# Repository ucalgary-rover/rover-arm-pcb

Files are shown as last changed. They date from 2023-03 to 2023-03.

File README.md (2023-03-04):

# rover-arm-pcb

A custom robot arm control PCB for the 2023 SSRT rover.

## Features
* Onboard microcontroller breakout board, like an Arduino Mega or similar
* Controls up to:
    * 7x NEMA23 stepper motors
    * 2x servo motors
    * 7x limit switches
    * A spotlight
    * Other peripherals, like grip strength load cell sensors
* Per-motor current sensing capabilities
* Integrates with off-the-shelf stepper motor drivers (TB6560) and custom circuitry for high reliability and ease of assembly

## Methodology
* PCB is designed in KiCAD v7.0.
* PCB design is used as a teaching tool, so simplicity and likelihood of success was prioritized

## Dependencies
https://github.com/Alarm-Siren/arduino-kicad-library

## Opportunities for Impovement
* Use an encoder/decoder for the EN pins, instead of using so many pins on the microcontroller.

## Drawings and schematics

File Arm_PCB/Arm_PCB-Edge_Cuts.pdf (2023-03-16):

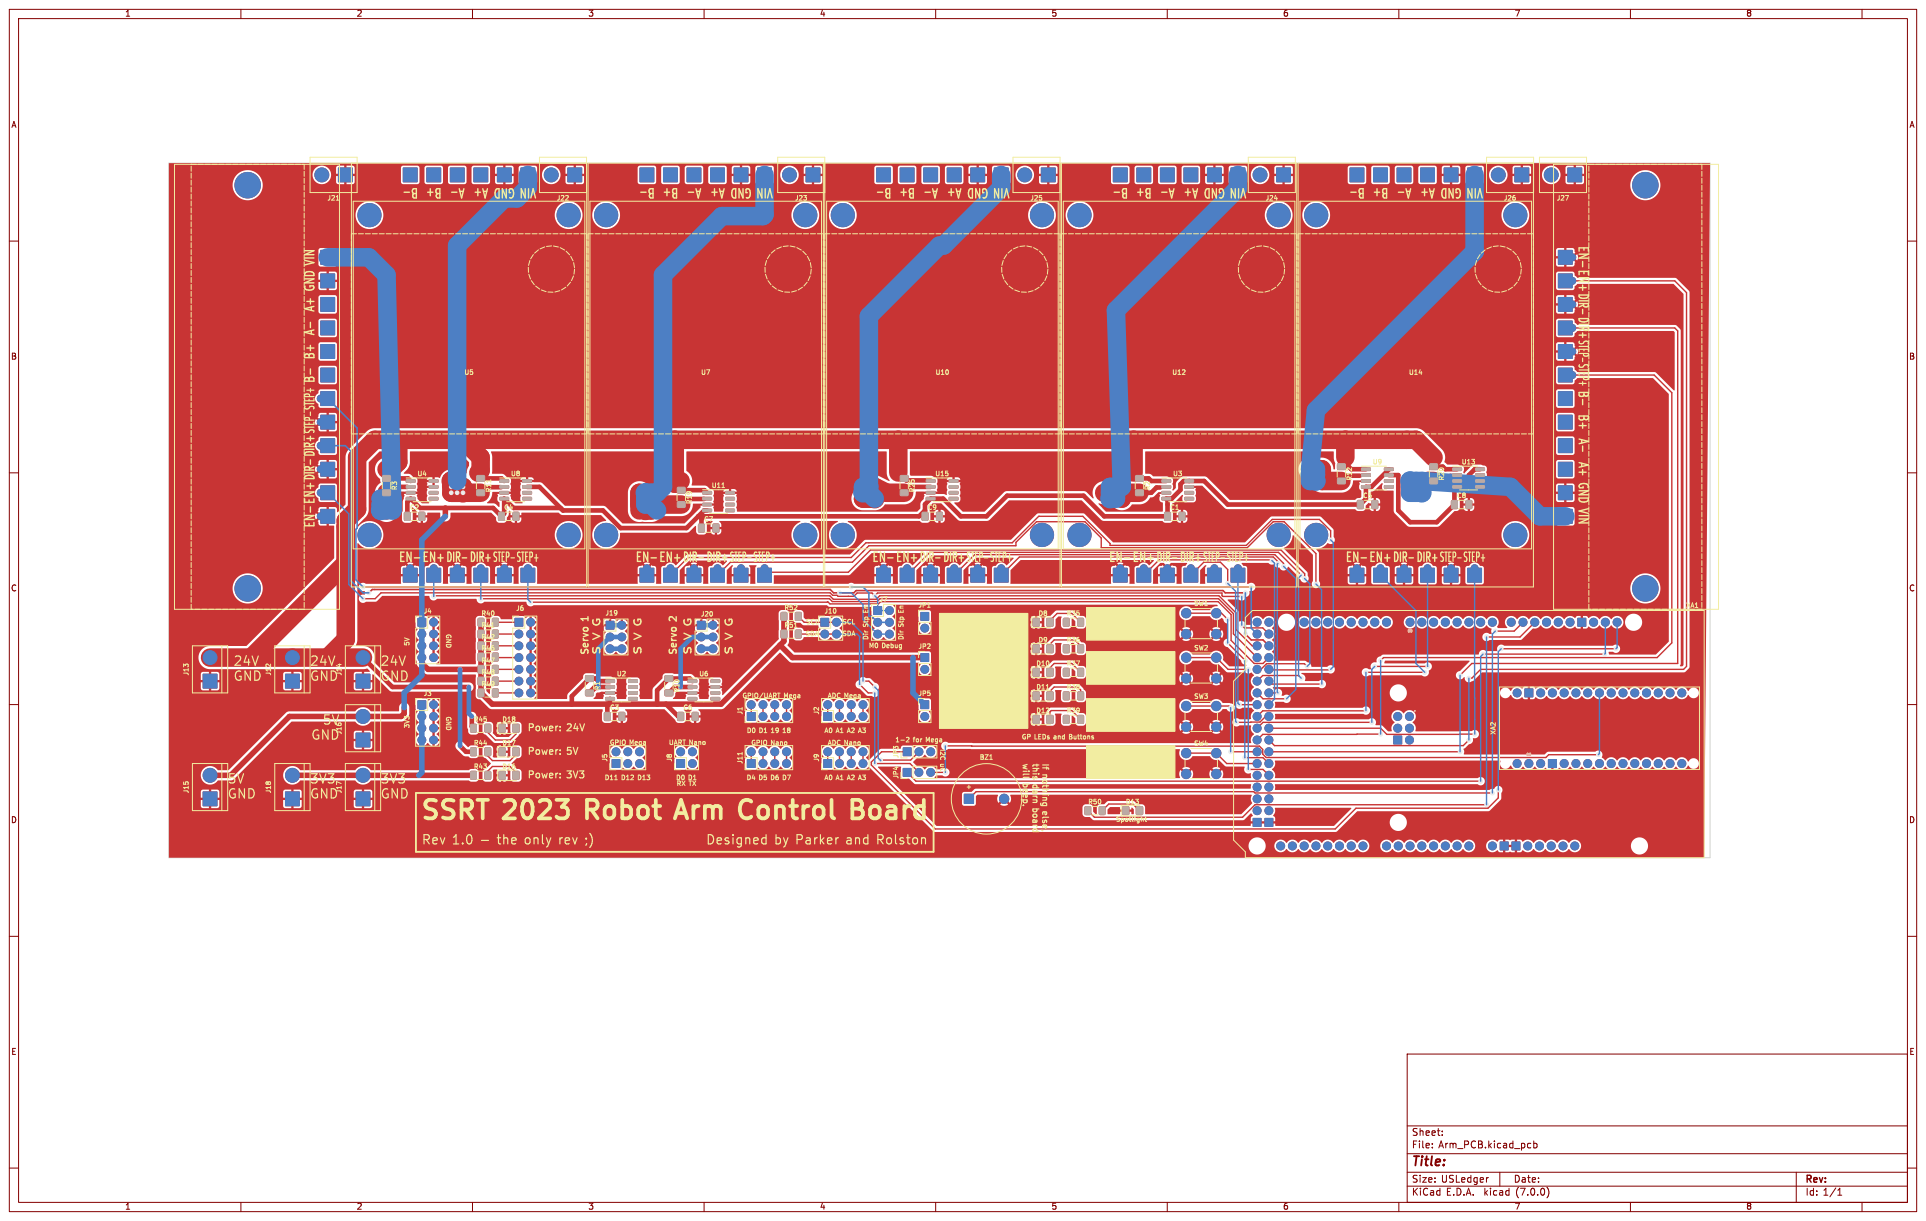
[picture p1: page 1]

R48 DIR+ B- STEP+ B+ A- EN- VIN STEP- GND A+ DIR- EN+

Id: 1/1 Title: File: Arm_PCB.kicad_pcb Sheet:

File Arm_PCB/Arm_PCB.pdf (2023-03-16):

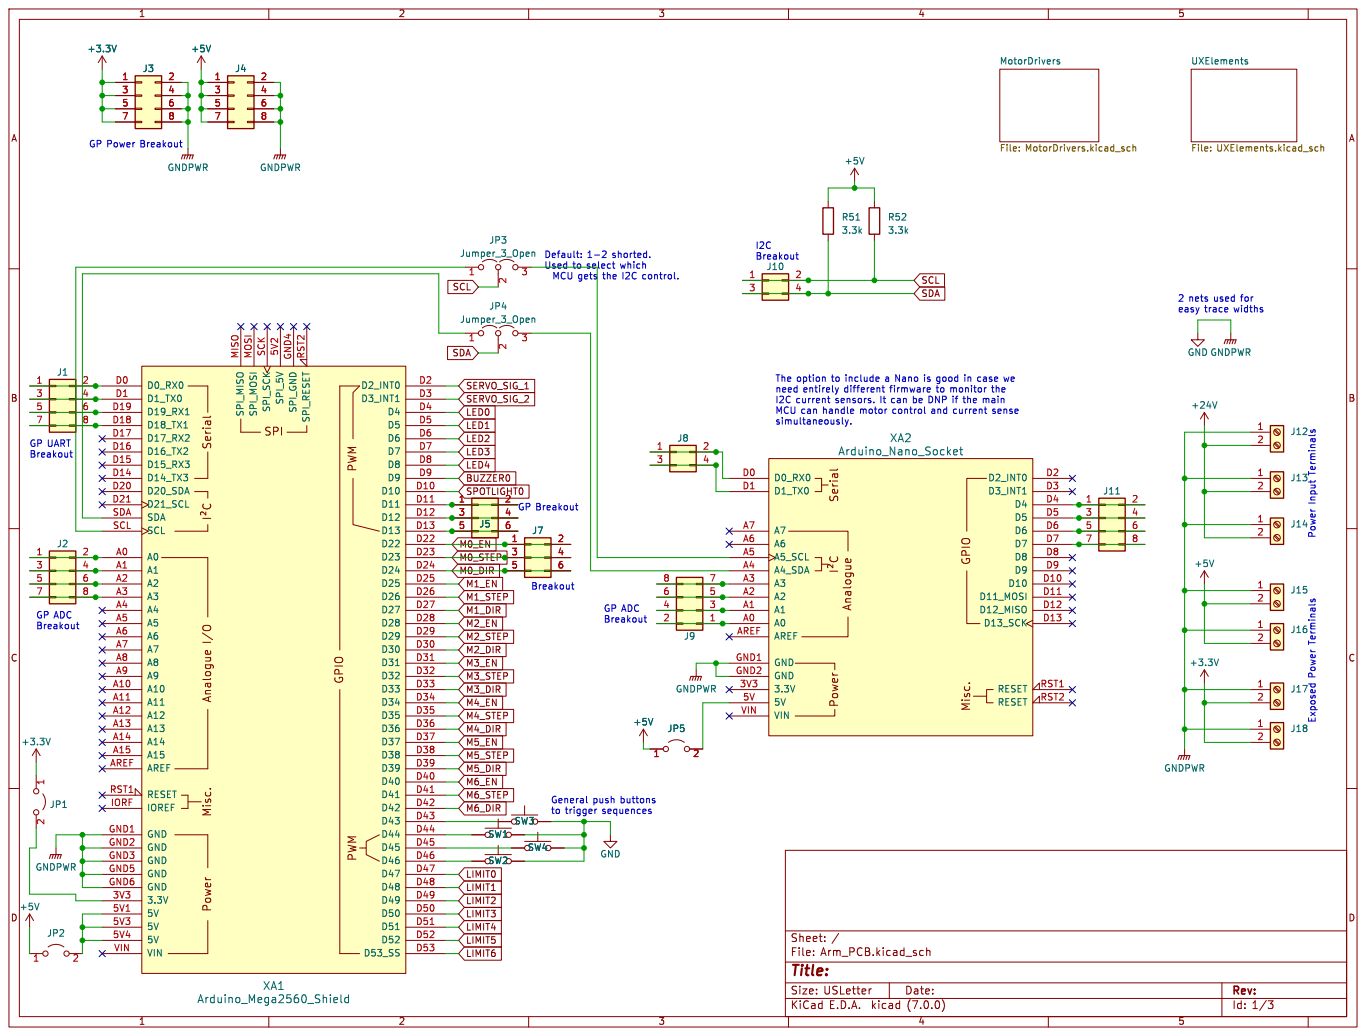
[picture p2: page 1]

GP Power Breakout GP ADC

UXElements File: UXElements.kicad_sch MotorDrivers File: MotorDrivers.kicad_sch +3.3V

I2C current sensors. It can be DNP if the main MCU can handle motor control and current sense

Id: 1/3 Title: File: Arm_PCB.kicad_sch Sheet: /

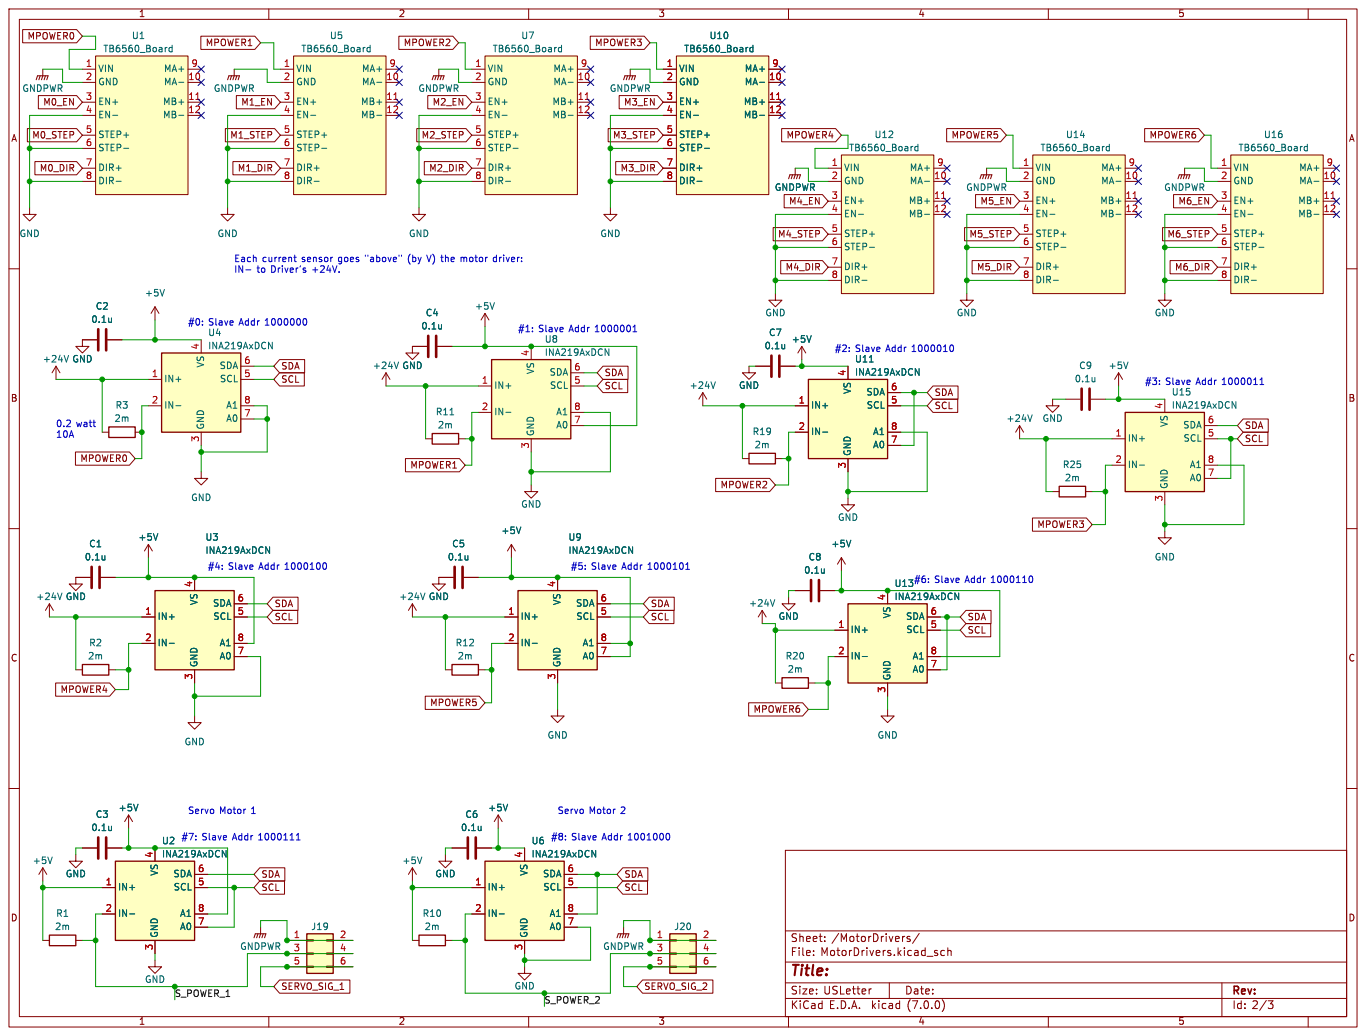
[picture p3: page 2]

#3: Slave Addr 1000011 Each current sensor goes "above" (by V) the motor driver:

#5: Slave Addr 1000101 Servo Motor 2

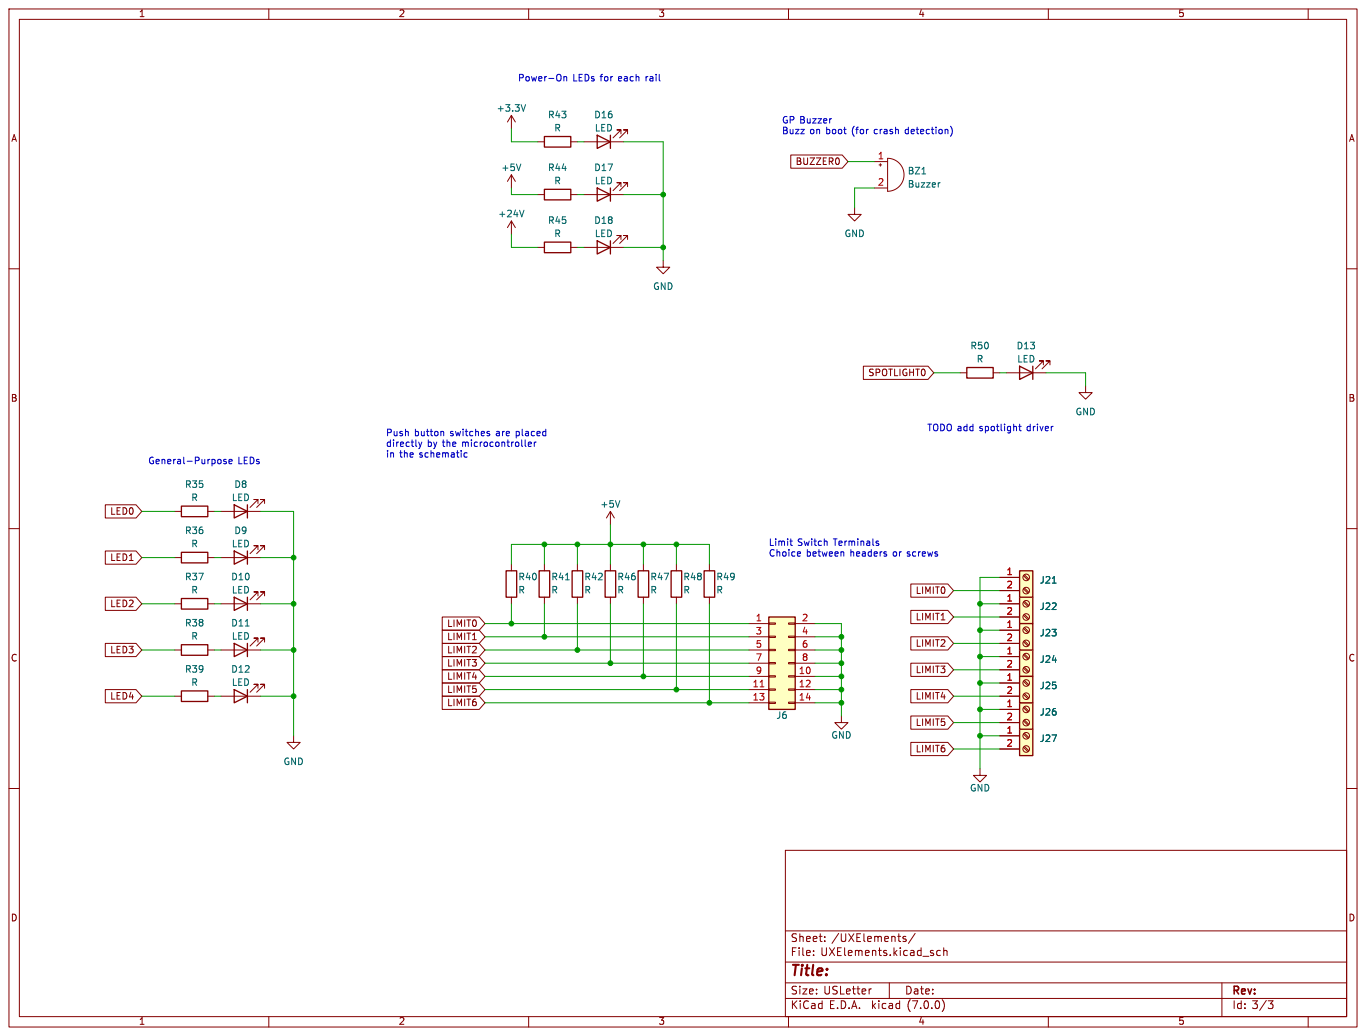
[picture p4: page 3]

directly by the microcontroller

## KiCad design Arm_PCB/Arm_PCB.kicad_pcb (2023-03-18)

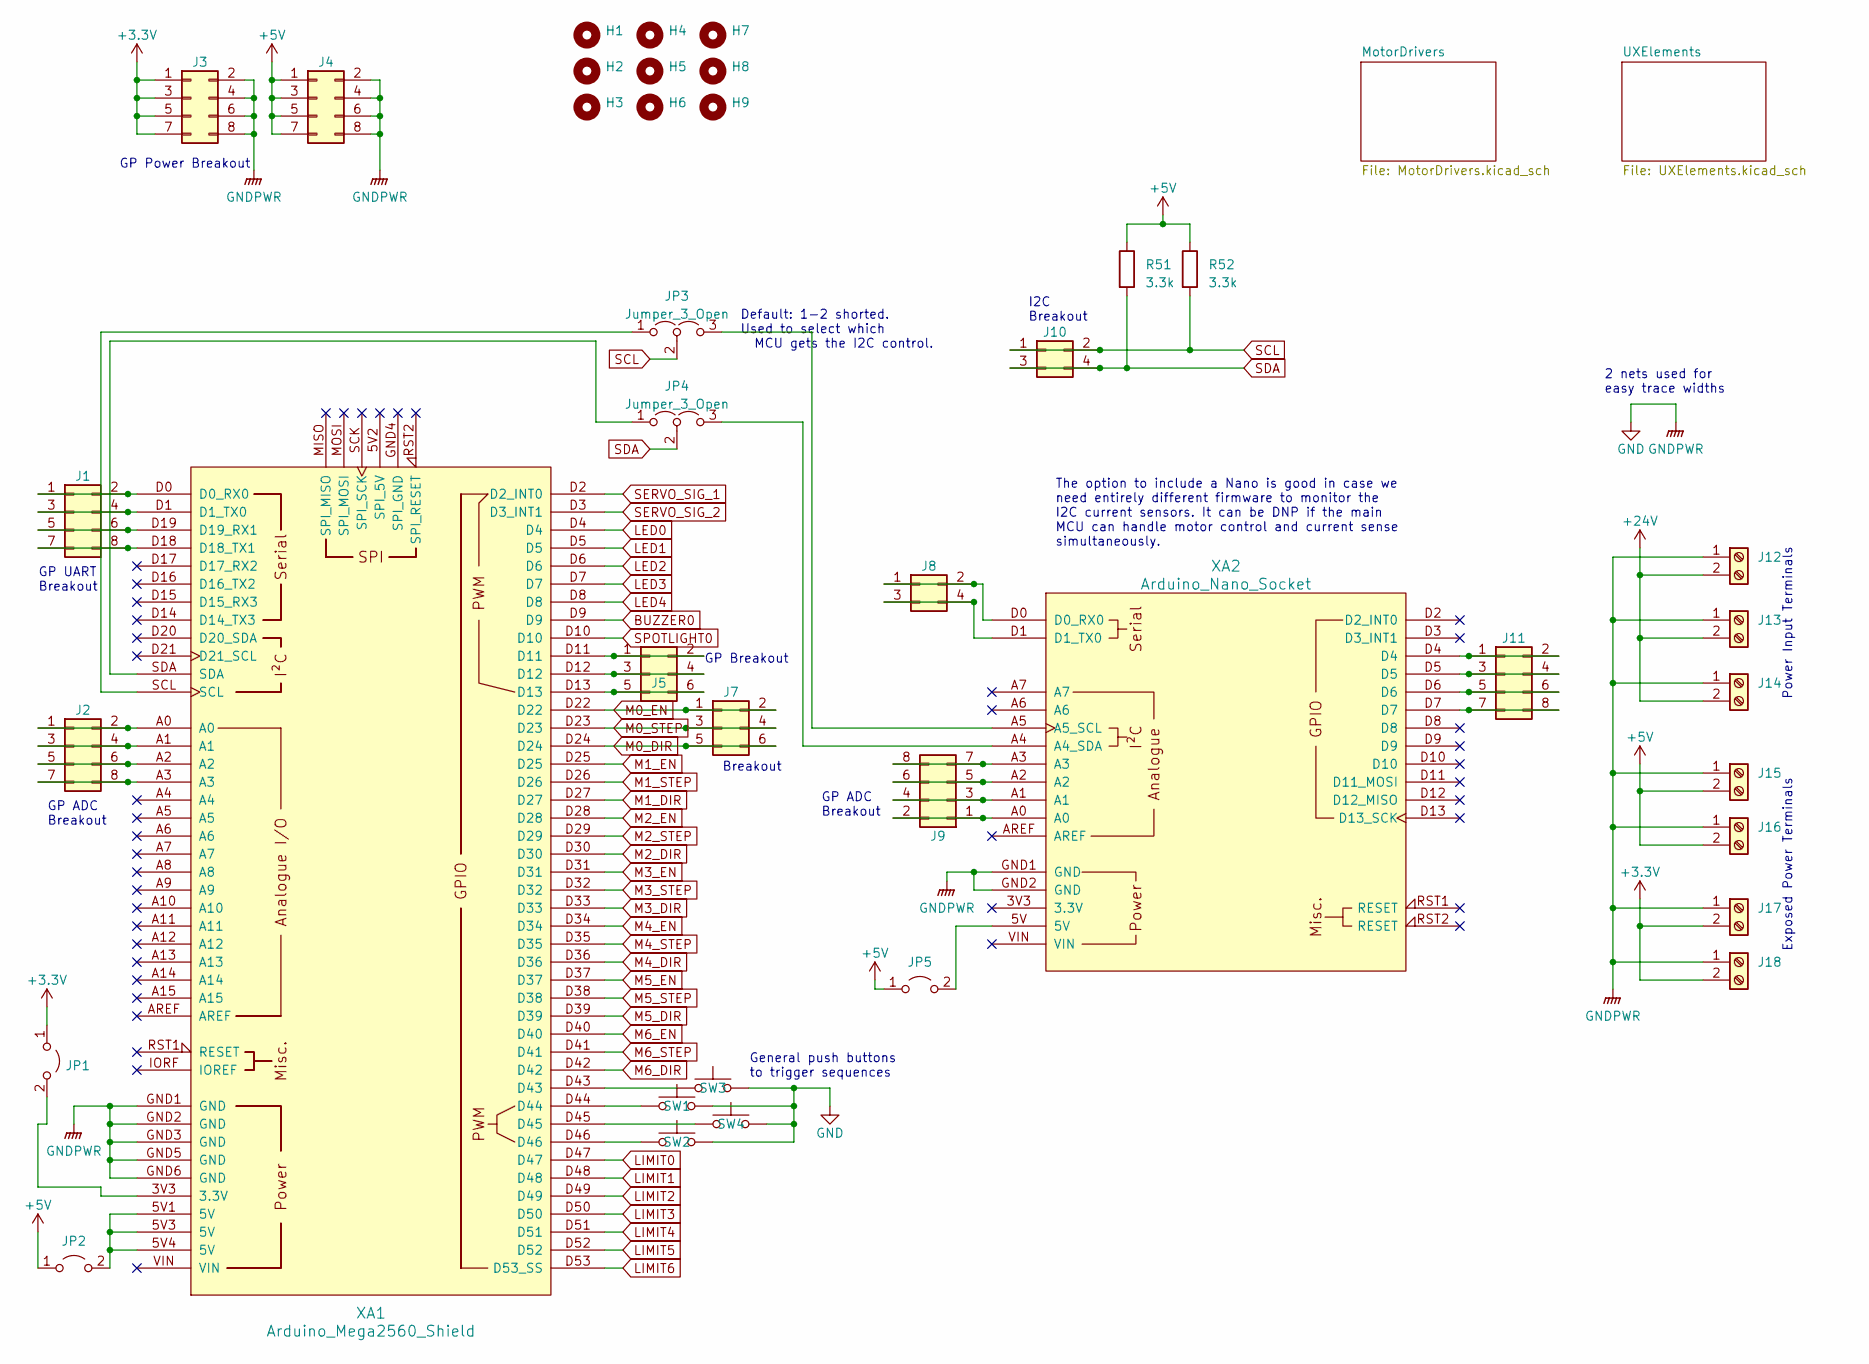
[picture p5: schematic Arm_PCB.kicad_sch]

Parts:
H1, H2, H3, H4, H5, H6, H7, H8, H9: MountingHole; MountingHole_4.3mm_M4
J1, J2, J3, J4, J9, J11: Conn_02x04_Counter_Clockwise; PinHeader_2x04_P2.54mm_Vertical
J5, J7: Conn_02x03_Counter_Clockwise; PinHeader_2x03_P2.54mm_Vertical
J8, J10: Conn_02x02_Counter_Clockwise; PinHeader_2x02_P2.54mm_Vertical
J12, J13, J14, J15, J16, J17, J18: Screw_Terminal_01x02; TerminalBlock_bornier-2_P5.08mm
JP1, JP2, JP5: Jumper_2_Open; PinHeader_1x02_P2.54mm_Vertical
JP3, JP4: Jumper_3_Open; PinHeader_1x03_P2.54mm_Vertical
R51, R52: 3.3k; R_1206_3216Metric_Pad1.30x1.75mm_HandSolder
SW1, SW2, SW3, SW4: SW_Push; SW_PUSH_6mm
XA1: Arduino_Mega2560_Shield
XA2: Arduino_Nano_Socket

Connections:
+3.3V: J3.1, J3.3, J3.5, J3.7, J17.2, J18.2, JP1.1 (A); also elsewhere on the board
+5V: J4.1, J4.3, J4.5, J4.7, J15.2, J16.2, JP2.1 (A), JP5.1 (A), R51.1, R52.1; also elsewhere on the board
+24V: J12.2, J13.2, J14.2; also elsewhere on the board
BUZZER0: XA1.D9; also elsewhere on the board
GND: J3.2, J3.4, J3.6, J3.8, J4.2, J4.4, J4.6, J4.8, J12.1, J13.1, J14.1, J15.1, J16.1, J17.1, J18.1, SW1.2, SW2.2, SW3.2, SW4.2, XA1.GND1 (GND), XA1.GND2 (GND), XA1.GND3 (GND), XA1.GND5 (GND), XA1.GND6 (GND), XA2.GND1 (GND), XA2.GND2 (GND); also elsewhere on the board
LED0: XA1.D4; also elsewhere on the board
LED1: XA1.D5; also elsewhere on the board
LED2: XA1.D6; also elsewhere on the board
LED3: XA1.D7; also elsewhere on the board
LED4: XA1.D8; also elsewhere on the board
LIMIT0: XA1.D47; also elsewhere on the board
LIMIT1: XA1.D48; also elsewhere on the board
LIMIT2: XA1.D49; also elsewhere on the board
LIMIT3: XA1.D50; also elsewhere on the board
LIMIT4: XA1.D51; also elsewhere on the board
LIMIT5: XA1.D52; also elsewhere on the board
LIMIT6: XA1.D53 (D53_SS); also elsewhere on the board
M0_DIR: J7.5, J7.6, XA1.D24; also elsewhere on the board
M0_EN: J7.1, J7.2, XA1.D22; also elsewhere on the board
M0_STEP: J7.3, J7.4, XA1.D23; also elsewhere on the board
M1_DIR: XA1.D27; also elsewhere on the board
M1_EN: XA1.D25; also elsewhere on the board
M1_STEP: XA1.D26; also elsewhere on the board
M2_DIR: XA1.D30; also elsewhere on the board
M2_EN: XA1.D28; also elsewhere on the board
M2_STEP: XA1.D29; also elsewhere on the board
M3_DIR: XA1.D33; also elsewhere on the board
M3_EN: XA1.D31; also elsewhere on the board
M3_STEP: XA1.D32; also elsewhere on the board
M4_DIR: XA1.D36; also elsewhere on the board
M4_EN: XA1.D34; also elsewhere on the board
M4_STEP: XA1.D35; also elsewhere on the board
M5_DIR: XA1.D39; also elsewhere on the board
M5_EN: XA1.D37; also elsewhere on the board
M5_STEP: XA1.D38; also elsewhere on the board
M6_DIR: XA1.D42; also elsewhere on the board
M6_EN: XA1.D40; also elsewhere on the board
M6_STEP: XA1.D41; also elsewhere on the board
unnamed: J1.1, J1.2, XA1.D0 (D0_RX0)
unnamed: J1.3, J1.4, XA1.D1 (D1_TX0)
unnamed: J1.5, J1.6, XA1.D19 (D19_RX1)
unnamed: J1.7, J1.8, XA1.D18 (D18_TX1)
unnamed: J2.1, J2.2, XA1.A0
unnamed: J2.3, J2.4, XA1.A1
unnamed: J2.5, J2.6, XA1.A2
unnamed: J2.7, J2.8, XA1.A3
unnamed: J5.1, J5.2, XA1.D11
unnamed: J5.3, J5.4, XA1.D12
unnamed: J5.5, J5.6, XA1.D13
unnamed: J8.1, J8.2, XA2.D0 (D0_RX0)
unnamed: J8.3, J8.4, XA2.D1 (D1_TX0)
unnamed: J9.1, J9.2, XA2.A0
unnamed: J9.3, J9.4, XA2.A1
unnamed: J9.5, J9.6, XA2.A2
unnamed: J9.7, J9.8, XA2.A3
unnamed: J11.1, J11.2, XA2.D4
unnamed: J11.3, J11.4, XA2.D5
unnamed: J11.5, J11.6, XA2.D6
unnamed: J11.7, J11.8, XA2.D7
unnamed: JP1.2 (B), XA1.3V3 (3.3V)
unnamed: JP2.2 (B), XA1.5V1 (5V), XA1.5V3 (5V), XA1.5V4 (5V)
unnamed: JP3.1 (A), XA1.SCL
unnamed: JP3.3 (B), XA2.A5 (A5_SCL)
unnamed: JP4.1 (A), XA1.SDA
unnamed: JP4.3 (B), XA2.A4 (A4_SDA)
unnamed: JP5.2 (B), XA2.5V
unnamed: SW1.1, XA1.D44
unnamed: SW2.1, XA1.D46
unnamed: SW3.1, XA1.D43
unnamed: SW4.1, XA1.D45
SCL: J10.1, J10.2, JP3.2 (C), R52.2; also elsewhere on the board
SDA: J10.3, J10.4, JP4.2 (C), R51.2; also elsewhere on the board
SERVO_SIG_1: XA1.D2 (D2_INT0); also elsewhere on the board
SERVO_SIG_2: XA1.D3 (D3_INT1); also elsewhere on the board
SPOTLIGHT0: XA1.D10; also elsewhere on the board

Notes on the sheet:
Exposed Power Terminals
The option to include a Nano is good in case we need entirely different firmware to monitor the I2C current sensors. It can be DNP if the main MCU can handle motor control and current sense simultaneously.
General push buttons to trigger sequences
GP UART Breakout
GP Breakout
Default: 1-2 shorted. Used to select which MCU gets the I2C control.
2 nets used for easy trace widths
GP Power Breakout
GP ADC Breakout
I2C Breakout
Breakout
Power Input Terminals

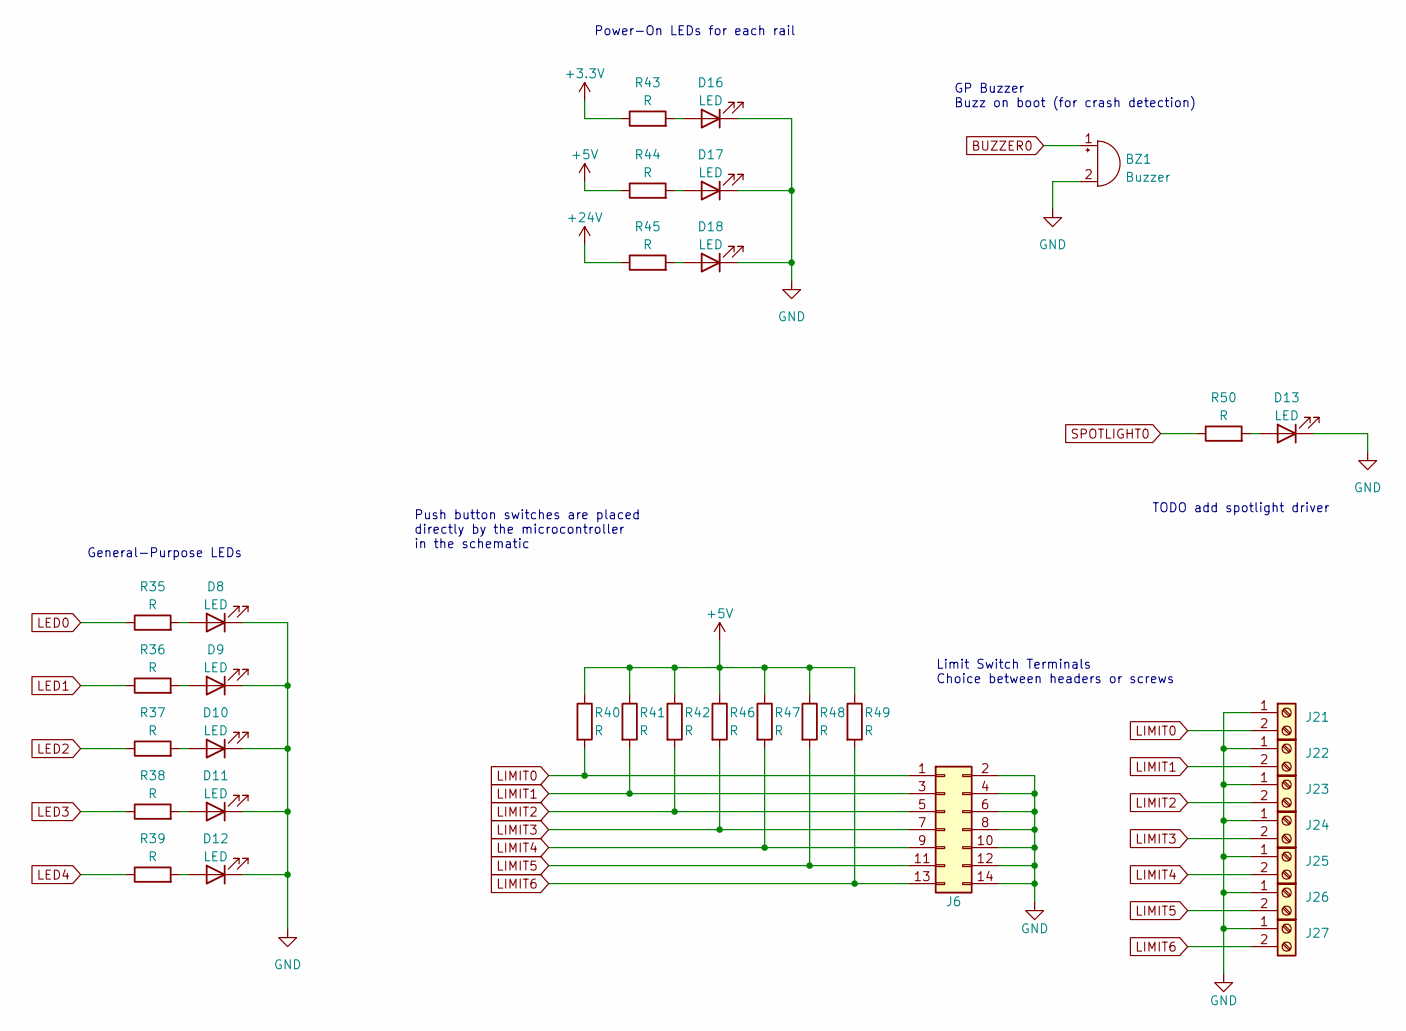
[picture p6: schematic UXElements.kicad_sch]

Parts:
BZ1: Buzzer; Buzzer_15x7.5RM7.6
D8, D9, D10, D11, D12, D13, D16, D17, D18: LED; LED_1206_3216Metric_Pad1.42x1.75mm_HandSolder
J6: Conn_02x07_Counter_Clockwise; PinHeader_2x07_P2.54mm_Vertical
J21, J22, J23, J24, J25, J26, J27: Screw_Terminal_01x02; TerminalBlock_bornier-2_P5.08mm
R35, R36, R37, R38, R39, R40, R41, R42, R43, R44, R45, R46, R47, R48, R49, R50: R; R_1206_3216Metric_Pad1.30x1.75mm_HandSolder

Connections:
+3.3V: R43.1; also elsewhere on the board
+5V: R40.1, R41.1, R42.1, R44.1, R46.1, R47.1, R48.1, R49.1; also elsewhere on the board
+24V: R45.1; also elsewhere on the board
BUZZER0: BZ1.1 (-); also elsewhere on the board
GND: BZ1.2 (+), D8.1 (K), D9.1 (K), D10.1 (K), D11.1 (K), D12.1 (K), D13.1 (K), D16.1 (K), D17.1 (K), D18.1 (K), J6.2, J6.4, J6.6, J6.8, J6.10, J6.12, J6.14, J21.1, J22.1, J23.1, J24.1, J25.1, J26.1, J27.1; also elsewhere on the board
LED0: R35.1; also elsewhere on the board
LED1: R36.1; also elsewhere on the board
LED2: R37.1; also elsewhere on the board
LED3: R38.1; also elsewhere on the board
LED4: R39.1; also elsewhere on the board
LIMIT0: J6.1, J21.2, R40.2; also elsewhere on the board
LIMIT1: J6.3, J22.2, R41.2; also elsewhere on the board
LIMIT2: J6.5, J23.2, R42.2; also elsewhere on the board
LIMIT3: J6.7, J24.2, R46.2; also elsewhere on the board
LIMIT4: J6.9, J25.2, R47.2; also elsewhere on the board
LIMIT5: J6.11, J26.2, R48.2; also elsewhere on the board
LIMIT6: J6.13, J27.2, R49.2; also elsewhere on the board
unnamed: D8.2 (A), R35.2
unnamed: D9.2 (A), R36.2
unnamed: D10.2 (A), R37.2
unnamed: D11.2 (A), R38.2
unnamed: D12.2 (A), R39.2
unnamed: D13.2 (A), R50.2
unnamed: D16.2 (A), R43.2
unnamed: D17.2 (A), R44.2
unnamed: D18.2 (A), R45.2
SPOTLIGHT0: R50.1; also elsewhere on the board

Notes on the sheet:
Push button switches are placed directly by the microcontroller in the schematic
Power-On LEDs for each rail
TODO add spotlight driver
Limit Switch Terminals Choice between headers or screws
GP Buzzer Buzz on boot (for crash detection)
General-Purpose LEDs

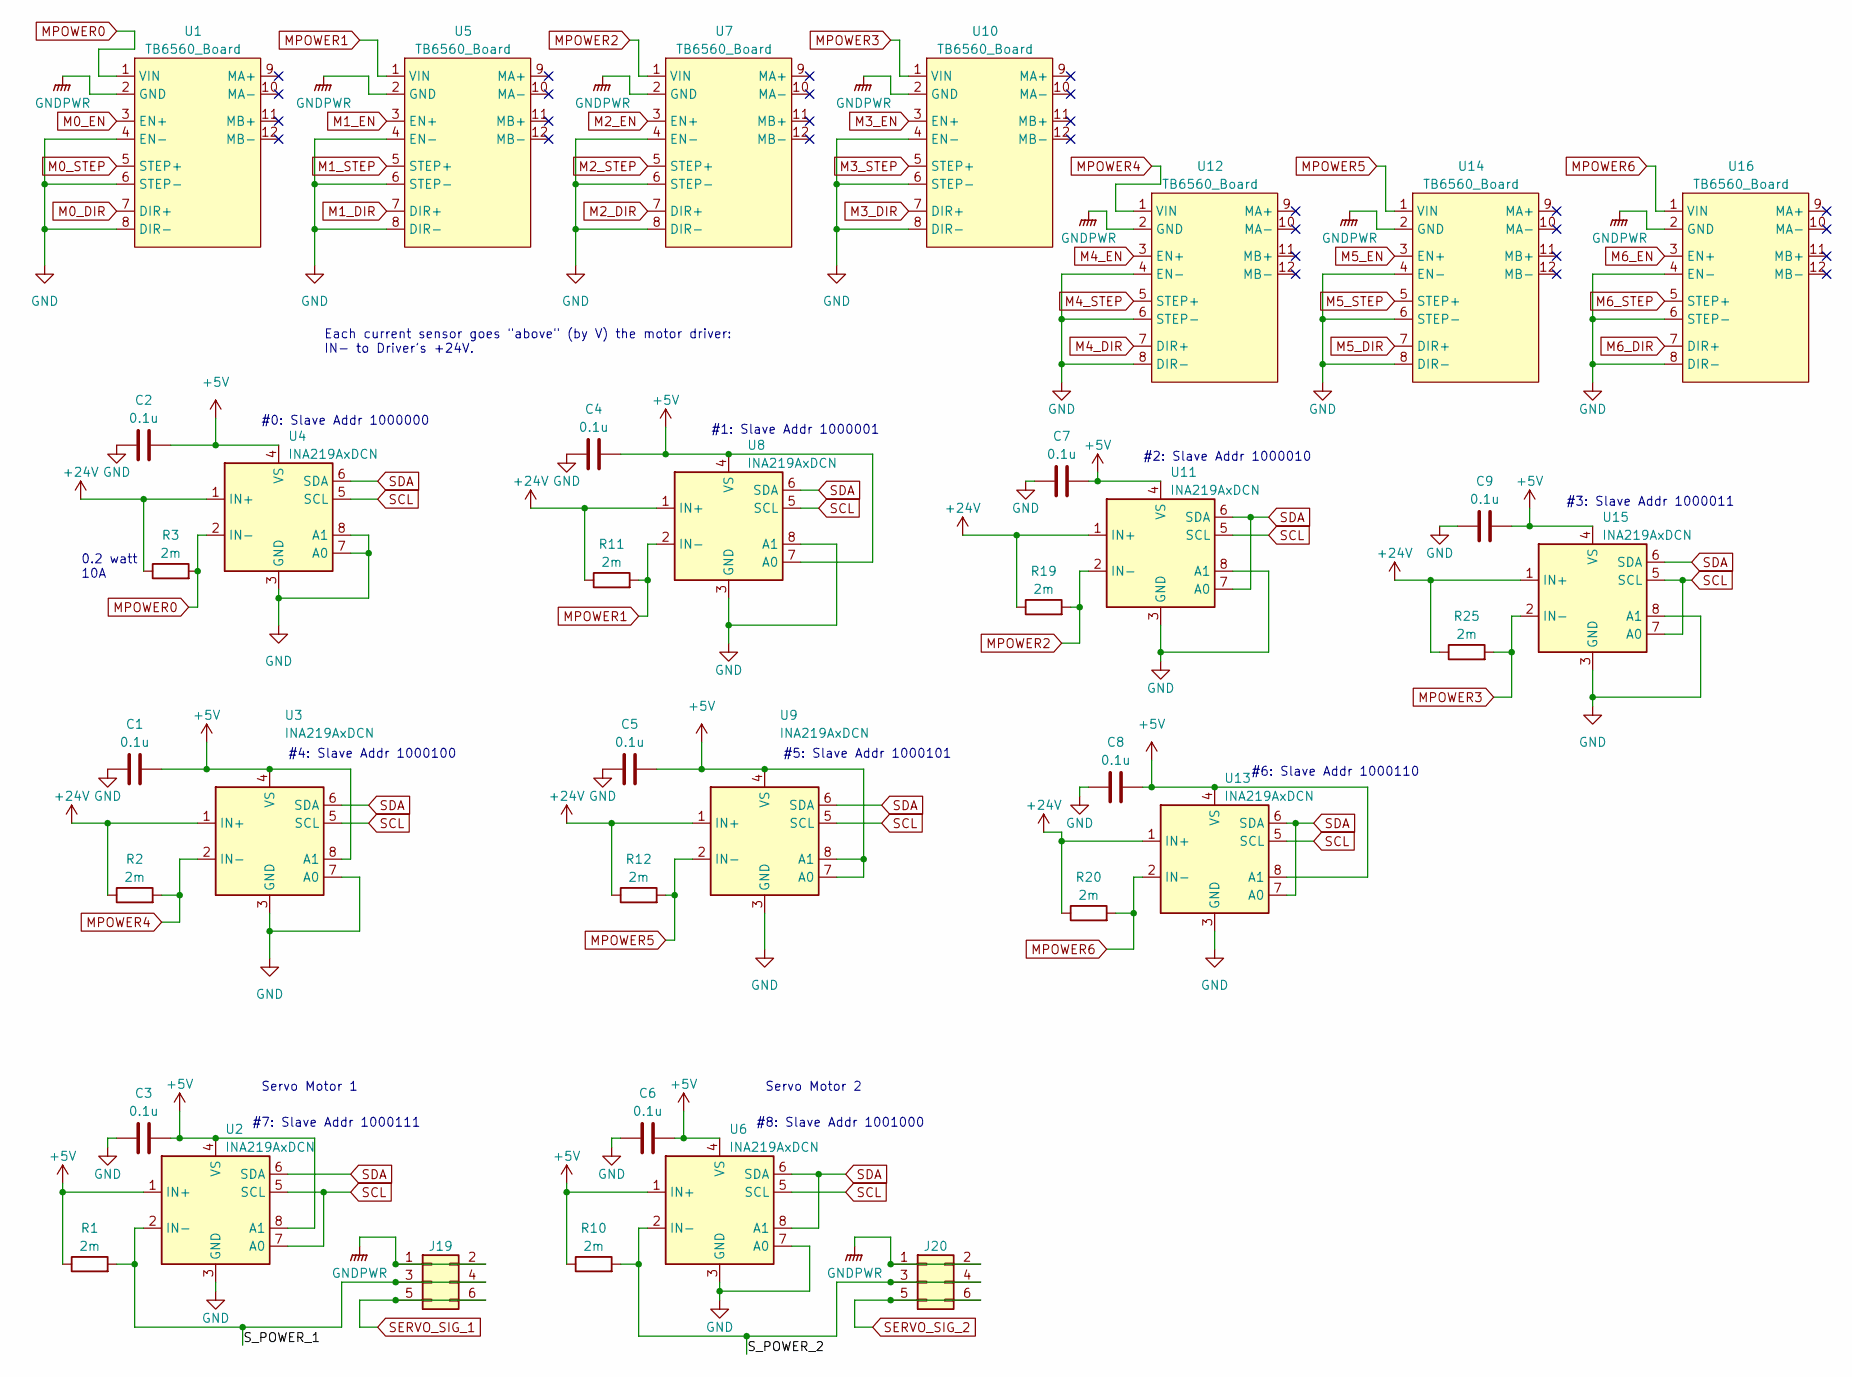
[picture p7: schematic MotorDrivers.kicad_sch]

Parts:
C1, C2, C3, C4, C5, C6, C7, C8, C9: 0.1u; C_1206_3216Metric_Pad1.33x1.80mm_HandSolder
J19, J20: Conn_02x03_Counter_Clockwise; PinHeader_2x03_P2.54mm_Vertical
R1, R2, R3, R10, R11, R12, R19, R20, R25: 2m; R_1206_3216Metric_Pad1.30x1.75mm_HandSolder
U1, U16: TB6560_Board; TB6600_Breakout
U2, U3, U4, U6, U8, U9, U11, U13, U15: INA219AxDCN; SOIC-8_3.9x4.9mm_P1.27mm
U5, U7, U10, U12, U14: TB6560_Board; TB6560_Breakout

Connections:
+5V: C1.1, C2.1, C3.1, C4.1, C5.1, C6.1, C7.1, C8.1, C9.1, R1.1, R10.1, U2.1 (IN+), U2.4 (VS), U2.8 (A1), U3.4 (VS), U3.8 (A1), U4.4 (VS), U6.1 (IN+), U6.4 (VS), U8.4 (VS), U8.7 (A0), U9.4 (VS), U9.7 (A0), U9.8 (A1), U11.4 (VS), U13.4 (VS), U13.8 (A1), U15.4 (VS); also elsewhere on the board
+24V: R2.1, R3.1, R11.1, R12.1, R19.1, R20.1, R25.1, U3.1 (IN+), U4.1 (IN+), U8.1 (IN+), U9.1 (IN+), U11.1 (IN+), U13.1 (IN+), U15.1 (IN+); also elsewhere on the board
/MotorDrivers/S_POWER_1: J19.3, J19.4, R1.2, U2.2 (IN-)
/MotorDrivers/S_POWER_2: J20.3, J20.4, R10.2, U6.2 (IN-)
GND: C1.2, C2.2, C3.2, C4.2, C5.2, C6.2, C7.2, C8.2, C9.2, J19.1, J19.2, J20.1, J20.2, U1.2 (GND), U1.4 (EN-), U1.6 (STEP-), U1.8 (DIR-), U2.3 (GND), U3.3 (GND), U3.7 (A0), U4.3 (GND), U4.7 (A0), U4.8 (A1), U5.2 (GND), U5.4 (EN-), U5.6 (STEP-), U5.8 (DIR-), U6.3 (GND), U6.7 (A0), U7.2 (GND), U7.4 (EN-), U7.6 (STEP-), U7.8 (DIR-), U8.3 (GND), U8.8 (A1), U9.3 (GND), U10.2 (GND), U10.4 (EN-), U10.6 (STEP-), U10.8 (DIR-), U11.3 (GND), U11.8 (A1), U12.2 (GND), U12.4 (EN-), U12.6 (STEP-), U12.8 (DIR-), U13.3 (GND), U14.2 (GND), U14.4 (EN-), U14.6 (STEP-), U14.8 (DIR-), U15.3 (GND), U15.8 (A1), U16.2 (GND), U16.4 (EN-), U16.6 (STEP-), U16.8 (DIR-); also elsewhere on the board
M0_DIR: U1.7 (DIR+); also elsewhere on the board
M0_EN: U1.3 (EN+); also elsewhere on the board
M0_STEP: U1.5 (STEP+); also elsewhere on the board
M1_DIR: U5.7 (DIR+); also elsewhere on the board
M1_EN: U5.3 (EN+); also elsewhere on the board
M1_STEP: U5.5 (STEP+); also elsewhere on the board
M2_DIR: U7.7 (DIR+); also elsewhere on the board
M2_EN: U7.3 (EN+); also elsewhere on the board
M2_STEP: U7.5 (STEP+); also elsewhere on the board
M3_DIR: U10.7 (DIR+); also elsewhere on the board
M3_EN: U10.3 (EN+); also elsewhere on the board
M3_STEP: U10.5 (STEP+); also elsewhere on the board
M4_DIR: U12.7 (DIR+); also elsewhere on the board
M4_EN: U12.3 (EN+); also elsewhere on the board
M4_STEP: U12.5 (STEP+); also elsewhere on the board
M5_DIR: U14.7 (DIR+); also elsewhere on the board
M5_EN: U14.3 (EN+); also elsewhere on the board
M5_STEP: U14.5 (STEP+); also elsewhere on the board
M6_DIR: U16.7 (DIR+); also elsewhere on the board
M6_EN: U16.3 (EN+); also elsewhere on the board
M6_STEP: U16.5 (STEP+); also elsewhere on the board
MPOWER0: R3.2, U1.1 (VIN), U4.2 (IN-)
MPOWER1: R11.2, U5.1 (VIN), U8.2 (IN-)
MPOWER2: R19.2, U7.1 (VIN), U11.2 (IN-)
MPOWER3: R25.2, U10.1 (VIN), U15.2 (IN-)
MPOWER4: R2.2, U3.2 (IN-), U12.1 (VIN)
MPOWER5: R12.2, U9.2 (IN-), U14.1 (VIN)
MPOWER6: R20.2, U13.2 (IN-), U16.1 (VIN)
SCL: U2.5 (SCL), U2.7 (A0), U3.5 (SCL), U4.5 (SCL), U6.5 (SCL), U8.5 (SCL), U9.5 (SCL), U11.5 (SCL), U13.5 (SCL), U15.5 (SCL), U15.7 (A0); also elsewhere on the board
SDA: U2.6 (SDA), U3.6 (SDA), U4.6 (SDA), U6.6 (SDA), U6.8 (A1), U8.6 (SDA), U9.6 (SDA), U11.6 (SDA), U11.7 (A0), U13.6 (SDA), U13.7 (A0), U15.6 (SDA); also elsewhere on the board
SERVO_SIG_1: J19.5, J19.6; also elsewhere on the board
SERVO_SIG_2: J20.5, J20.6; also elsewhere on the board

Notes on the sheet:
#1: Slave Addr 1000001
Servo Motor 2
Each current sensor goes "above" (by V) the motor driver: IN- to Driver's +24V.
Servo Motor 1
#8: Slave Addr 1001000
#0: Slave Addr 1000000
0.2 watt 10A
#7: Slave Addr 1000111
#6: Slave Addr 1000110
#2: Slave Addr 1000010
#3: Slave Addr 1000011
#5: Slave Addr 1000101
#4: Slave Addr 1000100

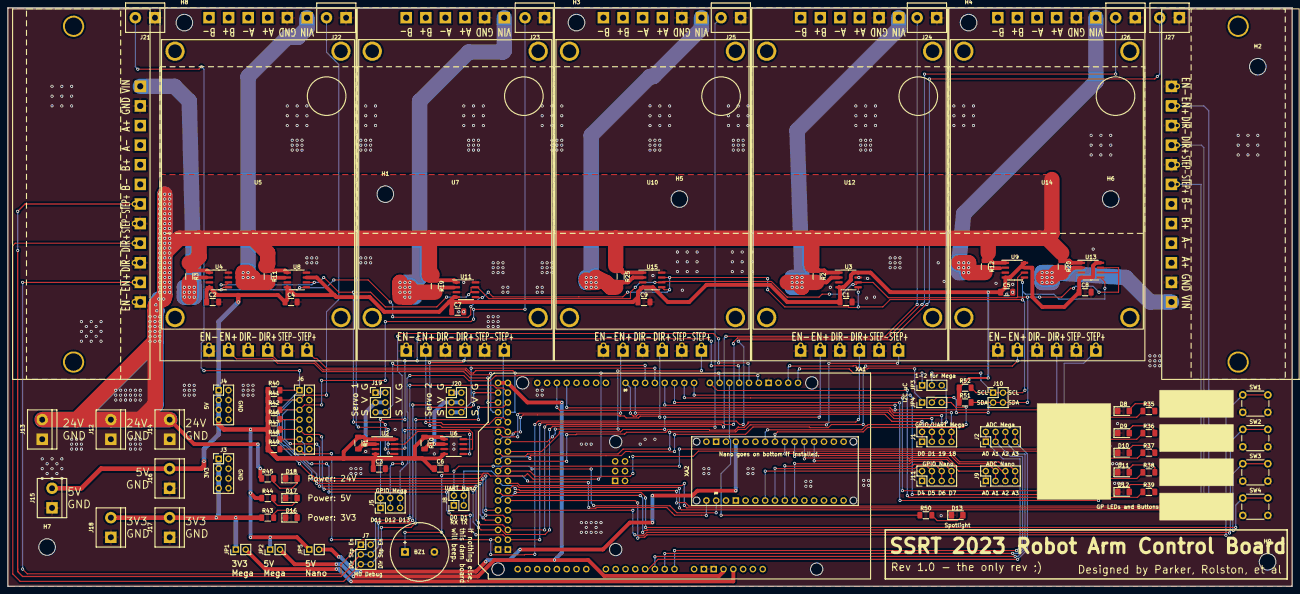
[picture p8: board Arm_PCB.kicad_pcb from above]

Board: 2 copper layers, 332.7 x 149.9 mm, 109 parts (1 on the bottom side), 93 nets.

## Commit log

2023-02-25 Add initial files
    [Arm_PCB.kicad_pcb, Arm_PCB.kicad_sch]
2023-02-25 Added motor controllers and the micro-controllers"
    [Arm_PCB.kicad_pcb, Arm_PCB.kicad_sch, MotorDrivers.kicad_sch]
2023-02-27 Added the INA219 schematics,fixed the TB6560 board, added LED for the EN pin on the microcontroller
    [Arm_PCB.kicad_sch, MotorDrivers.kicad_sch]
2023-03-03 Changes, migrate to KiCad v7
    [Arm_PCB.kicad_sch, MotorDrivers.kicad_sch, UXElements.kicad_sch]
2023-03-03 Changes, including UX and breakout pins
    [Arm_PCB.kicad_sch, MotorDrivers.kicad_sch, UXElements.kicad_sch]
2023-03-03 Add servo current sensors, etc.
    [Arm_PCB.kicad_sch, MotorDrivers.kicad_sch, UXElements.kicad_sch]
2023-03-04 Update footprint library
    [MotorDrivers.kicad_sch]
2023-03-04 Annotate all pages
    [Arm_PCB.kicad_sch, MotorDrivers.kicad_sch, UXElements.kicad_sch]
2023-03-04 Add annotations
    [Arm_PCB.kicad_sch, MotorDrivers.kicad_sch]
2023-03-04 Add spotlight and resistors on limit switches
    [Arm_PCB.kicad_sch, UXElements.kicad_sch]
2023-03-04 Added a basic footprint for the PCB
    [Arm_PCB.kicad_pcb, Arm_PCB.kicad_sch, MotorDrivers.kicad_sch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]
2023-03-05 Create good footprint for TB6560 driver
    [Arm_PCB.kicad_pcb, UXElements.kicad_sch]
2023-03-11 Grouped parts in the PCB sketch to begin routing
    [Arm_PCB.kicad_pcb]
2023-03-12 Continue layout, pick some components
    [Arm_PCB.kicad_pcb, Arm_PCB.kicad_sch, MotorDrivers.kicad_sch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]
2023-03-16 Add TB6600 footprint from online refs
2023-03-16 Footprint updates with new TB6600
    [Arm_PCB.kicad_pcb, MotorDrivers.kicad_sch]
2023-03-16 Remove resistors for setting I2C addrs
    [MotorDrivers.kicad_sch]
2023-03-16 Update layout
    [Arm_PCB.kicad_pcb]
2023-03-16 Start routing
    [Arm_PCB.kicad_pcb, Arm_PCB.kicad_sch]
2023-03-16 Route more
    [Arm_PCB.kicad_pcb, MotorDrivers.kicad_sch, UXElements.kicad_sch]
2023-03-16 Render PDFs
    [Arm_PCB.kicad_pcb]
2023-03-17 Route more, move uC to middle
    [Arm_PCB.kicad_pcb]
2023-03-17 Route nearly whole thing
    [Arm_PCB.kicad_pcb]
2023-03-17 Finish PCB haha
    [Arm_PCB.kicad_pcb]
2023-03-18 Add mounting holes, other minor changes
    [Arm_PCB.kicad_pcb, Arm_PCB.kicad_sch]
2023-03-18 minor trace width and thermal relief changes
2023-03-22 Add gerber
    [Arm_PCB-B_Cu.gbl, Arm_PCB-B_Mask.gbs, Arm_PCB-B_Paste.gbp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]
